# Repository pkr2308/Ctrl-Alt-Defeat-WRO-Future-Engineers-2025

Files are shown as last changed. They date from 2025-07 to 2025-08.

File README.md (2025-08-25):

# This repository has been moved to [CmdOptDefeat/fe25](https://github.com/CmdOptDefeat/fe25)

<picture>
  <source media="(prefers-color-scheme: dark)" srcset="https://github.com/pkr2308/Ctrl-Alt-Defeat-WRO-Future-Engineers-2025/blob/main/repo-assets/logo/ctrlaltdefeat-no-glow-no-bg-4096.png">
  <source media="(prefers-color-scheme: light)" srcset="https://github.com/pkr2308/Ctrl-Alt-Defeat-WRO-Future-Engineers-2025/blob/main/repo-assets/logo/ctrlaltdefeat-no-glow-no-bg-dark-4096.png">
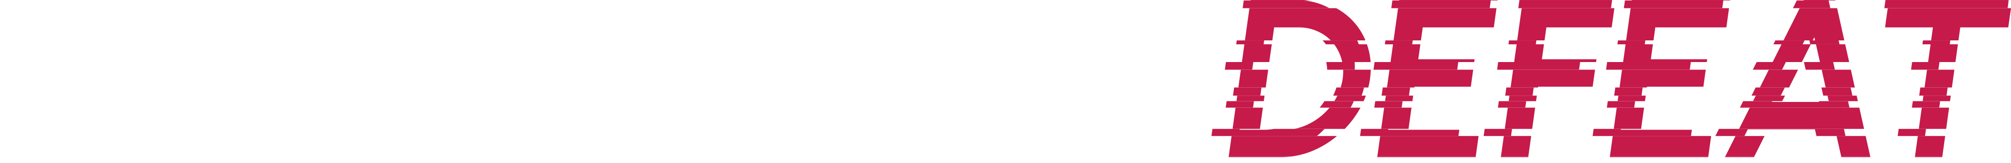
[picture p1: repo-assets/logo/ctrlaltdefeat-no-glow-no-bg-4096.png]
CTRL+ALT+DEFEAT Logo (updates based on your theme!)
  
</picture>

<br><br>Welcome to the repository for our entry in the WRO Future Engineers 2025 competition!
We are a team of 2 aspiring engineers building an autonomous robotic car using Raspberry Pi 5 & RP2040, equipped with various sensors and custom designs.

# About the Team
Adbhut Patil: TODO: expand 10th standard, interested in electronics, programming, aviation

Pranav Kiran Rajarathna: Pranav is currently sudying in the 11th grade(PCMC combination) and has been interested in Robotics for several years . He has participated in WRO in other categories in the past years. He was also part of Coding club in his school and built a few robotics projects for school events. His other interests include maths, physics, numismatics and history.

| __Team Photo__ |
|:-----------:|
|Team Photo|
| __Picture: Pranav (Left) and Adbhut (Right)__ |

# Project Overview
This project is our official entry for the Future Engineers category at the World Robot Olympiad 2025. Our goal is to construct a self-driving vehicle capable of navigating the track in both the Open and Obstacle Rounds. The programs are written in C++ and Python in the VSCode IDE, with the PlatformIO extension. OpenCV is used with the Raspberry Pi for object detection and navigation. This repository contains the programs, hardware description, schematics and design files of our solution.

# Hardware Components
- __Compute:__ Raspberry Pi 5 (main computer), Raspberry Pi 2040 (Waveshare RP2040-Zero, real-time control)
- __Sensors:__ 1D and 2D LiDAR, IMU, rotary encoders, Picamera
- __Actuators:__ N20 geared DC motor with encoder, MG996R 180° servo
- __Chassis:__ Commercially available base with 3D-printable additions (3D-design files included)
- __Electronics:__ Custom peripherals interface PCB for reliable connections to sensors

Note: The whole readme file is massive.
See [this section](https://github.com/pkr2308/Ctrl-Alt-Defeat-WRO-Future-Engineers-2025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) for more details about sensors on the peripherals interface board, and <link> for details about the RPi 5 and its sensors.

# Repository Structure
- [design-files](https://github.com/pkr2308/Ctrl-Alt-Defeat-WRO-Future-Engineers-2025/tree/main/design-files) : Contains the Bill of Materials, 3D-printable design files and hardware. Pictures and description of the robot and components are included.
- [initial-tests](https://github.com/pkr2308/Ctrl-Alt-Defeat-WRO-Future-Engineers-2025/tree/main/initial-tests) : Intial tests on various sensors to ensure accurate data collection and basic object detection algorithm.
- [hw](https://github.com/pkr2308/Ctrl-Alt-Defeat-WRO-Future-Engineers-2025/tree/main/hw) : Contains schematic and PCB files for the peripherals interface board.
- [sw](https://github.com/pkr2308/Ctrl-Alt-Defeat-WRO-Future-Engineers-2025/tree/main/sw) : Contains PlatformIO project for the peripherals interface board.
- [open-round](https://github.com/pkr2308/Ctrl-Alt-Defeat-WRO-Future-Engineers-2025/tree/main/open-round) : It contains the program files for the open round over various iterations and hardware setups. The final open round program is found in `sw/peripherals-board/src/divers`
- [repo-assets]() :
- [obstacle-round](https://github.com/pkr2308/Ctrl-Alt-Defeat-WRO-Future-Engineers-2025/tree/main/obstacle-round) : 
- [test-data-recordings/open-round](https://github.com/pkr2308/Ctrl-Alt-Defeat-WRO-Future-Engineers-2025/tree/main/test-data-recordings/open-round) : It contains data logs from various open round tests

> [!NOTE]
> Random files called `.lgd-nfy0` may be seen sometimes in varioues places. These were probably created by a typo a long time ago, and despite repeated deletion, they keep spawning everywhere in the Pi's cone of the repo! Just ignore them, if they occur. 

# System Architecture 

-	Raspberry Pi 5: It uses ROS2 and handles more complex tasks like object and colour detection, route planning, and the 2D LiDAR
-	RP2040 (Pi Pico): Handles real-time tasks (motor PID, encoder feedback, servo control, IMU, 1D LiDAR)
-	LiDARs: Used for detecting turn direction, obstacles and in parking
-	IMU: Gives yaw (and other orientations) of the robot in [0,360)
-	Motor/Servos: PWM and PI controls respectively for movement using sensor data, coordinated by the RP2040

## Mobility

- A commercially available metal [chassis base](https://www.elecrow.com/4wd-smart-car-robot-chassis-for-arduino-servo-steering.html) has been used with custom designed and printed parts. This chassis was selected mainly for its good steering system, mobility and customisabilty (there are lots of through holes through the base-frame). While the steering was retained, the remaining parts were custom designed.
- A link based steering system is used in the robot with a link-rod between the front wheel joints and another between a wheel joint and the servo. This steering system has been taken from the chassis without much modification due to its precision. A MG996R 180° servo has been used for the steering due to its high torque and accuracy, which improve mobility. 
- A single axle rear drive train is used for driving is used. A 200RPM N20 motor is used due to its speed and decent torque. A 1:1 gear ratio is used with a pair of brass gears. Bearings are used on the rear axle for smooth movement. A custom [rear drive holder](https://github.com/pkr2308/Ctrl-Alt-Defeat-WRO-Future-Engineers-2025/blob/main/design-files/N20%20Motor%20Holder.stl) is used to house all these parts.
- Both the servo and N20 motors are connected to the peripherals board. The servo is controlled using the standard library, while PWM is used for speed control of the motor.
- Turning Radius: Optimized for narrow WRO track corners, and is 32-33 cm.
- Build Choice Reasoning: Offers realistic car-like dynamics, ideal for FE challenge simulation.
[Design files](https://github.com/pkr2308/Ctrl-Alt-Defeat-WRO-Future-Engineers-2025/tree/main/design-files) contains all the other custom 3D-Design files (created on [TinkerCAD](https://www.tinkercad.com)) for mounting various compnents and systems onto the base chassis and one another.
[Robot assembly](https://github.com/pkr2308/Ctrl-Alt-Defeat-WRO-Future-Engineers-2025?tab=readme-ov-file#robot-assembly) instructions are below.
- Improvements: 
1. A uniform steering system. In the current model, the servo has to turn a greater angle left than right for the same angles of the wheels in each direction. This complicates driving algorithms to some extent. A better, but equally smooth steering system, maybe a rack-and-pinion, will solve these issues.
2. Better gear train. The current gears, though made of brass wear down quite easily for some unidentified reason. This causes slipping if there is more wear.
3. Reducing the turning radius. The current bot, while quite manoeuvrable has a large turn radius (almost 33-34cm). Reducing this would make taking tighter turns possible, improving error margins in the obstacle round. This can be done by bringing the drive train forward.

## Power

- A [Waveshare UPS Hat E](https://www.waveshare.com/wiki/UPS_HAT_(E)) is used for powering the robot. It uses 4 4000mAH 3.6V 21700 Li-ion batteries. (Different battery capacities may be used). All outputs are at 5V.
- The Pi is powered at a stable 5V via the POGO pins on the UPS Hat. The PiCamera and RPLidar are power from the Pi.
- The RP2040 and all connected sensors are powered through a USB A-C cable from the Pi to it.
- The total current draw for the obstacle round is around 600-630mA, and around 250-300mA for idle with the Pi.
- The peripherals board gets power directly from the UPS Hat through a USB-A cable that has been cut to get the power wires. This powers only the rear motor and steering servo.
- Improvements:
1. The UPS Hat that we are using has a weird anomaly. Although the batteries will have good voltage output and detected capacity, it will show the net remaining capacity to be very low. We have edited the code of the UPS library to not allow it run `sudo poweroff` when it misdetects such a situation.
2. Maybe not have the small switch on the board; closing it will cause these 2 systems to be connected, which could lead to some bad outcomes!

## Sensors

- __TFLuna LiDAR:__ These are 1D-LiDARs that are used to measure distances to the front, left, right (for driving) and back(parking) of the robot. They are connected to the RP2040. A separate section has been designed at the front of the robot to house all four LiDARs. Each LiDAR has 5 wires, grouped into 4+1 (I2C + GND) going into the peripherals board. These LiDARs were selected for their accuracy, small size and ease of use.
- __BNO055:__ This is the IMU we are using for orientation due to its reliability, accuracy and simplicity of use. It is connected to the RP2040, and is directly slotted into the peripherals board.
- __nRF24L01:__ This is the wireless module used for wireless communication during testing and debugging with the RP2040. Another custom module (telemetry board) is made for receiving the data. (Note : This is not plugged in for actual rounds). It is directly slotted into the peripherals board.
- __Motor encoders:__ The encoders give ticks each time they are trigerred by rotation of the motor shaft. Data from it is used for distance calculations. In our case, about 43 ticks corresponds to 1cm. The 4 encoder wires are grouped together and connected to the peripherals board.
- __Raspberry Pi Camera Module 3 Wide:__ It is used with the Pi for detecting the an obstacles. The camera is secured at four points for greater stability. With only two connection points, the camera could be easily turned due to the material properties of the Camera to Pi 5 connection wire. The higher mounting location allows it to detect obstacles from a large distance (almost 2m!) and plan accordingly. The Wide lens allows for a greater field of view. The NoIR version used to give odd red patches due to the lack of the IR filter in some test cases.
- __RPLidar A1:__ It is a 2D-LiDAR. It was supposed to be connected to the Pi and give distance all around the robot. However, we could not get it work Raspbian or any other OS. (It worked well with ROS though!) So, it is basically dead weight!
- Improvements: 
1. The RPLidar doesn't work well with the standard Raspbian OS on the Pi or with a computer, with values for many angles returned zero or being frozen. It seems to work fine on ROS though. Not sure what the issue is, but resoving this can improve ease of programming.
2. The 1D LiDARs are quite expensive. Ultrasonic sensors would have done for the sides.
3. The BNO055 does clock stretching, which causes issues on the I2C buses of most microcontrollers (thankfully not the RP2040). It also has a slight drifting tendency of a few degrees after a round. A IMU that does not have these issues and is easy to use will be more accurate and more flexible in use.

The [Bill of Materials](https://github.com/pkr2308/Ctrl-Alt-Defeat-WRO-Future-Engineers-2025/blob/main/design-files/Bill%20of%20Materials.md) contains all necessary parts/components and their sources.

## Obstacle Management

- This is done mainly using the camera feed from the PiCamera 3 Wide. The NoIR version tends to give red spot in places with lots of light due to lack of IR filter, which made it incompatible for this case.
- The OpenCV library (in Python3) is used for all the image manipulation and data extrapolation. HSV mode has been used for all the detecting, while images arer displayed in RGB. Sometimes, red may appear as blue due to use of BGR format used by camera to rercord. This is of no consequence, since it does not affect detection itself.
- Initially, the colour ranges for the obstacles, parking walls and side walls are identified. Interestingly, in our case, the 'magenta' parking walls show up as pure red.
- First, the region of interest (ROI) is taken as the bottom half of the feed (this is for our camera placement. May vary for other setups).
- Then, coloured masks (one each for red and green) are applied, followed by OpenCV's controur detection to detect surfaces. Data like position, height and width of the contours may be obtained from the other OpenCV methods.
- If the contours detected meet the required criteria (like size, height-width ratio), they are classified as obstacles. For our benefit, rectangles are drawn around the obstacles.
- Using the data available, including obstacle position, yaw and distance travelled, the required steering is calculated to pass the obstacle on the correct side, when not at a turn (Red - right, green - left)
- When the side chosen is preceded by a turn, the turn is initiated at a predefined distance from the wall ahead. (Ex: Clockwise round, green -> turn early)

Improvements:
1. The RPLidar might have been used effectively with better drivers with the standard Raspbian OS.
2. A more accurate formula to convert y-coordinate of obstacle obtained by the camera into actual distance

# Robot Assembly

It will be helpful to refer to the pictures of the completed model for the following steps. Most screws used are of 3M type (3mm dia.). At some places in our robot, internal hex screws are used in places where plus(+) screws of the right length were not available.
1. Add the front wheels and steering link to the robot
2. Attach the servo motor and connect it to the steering link
3. Print all design files
4. Attach the N20 motor onto the rear drive with brackets. Fit a gear onto the motor.
5. Cut the rear axle to the appropriate length (around 96mm) and attach the rear axle with wheels and gear onto the rear drive.
6. Mount the rear drive onto the chassis.
7. Attach 6 pillar screws of length 26mm in the back and 2 of length 22mm in the front (adjacent to the servo)
8. Attach the middle plate at the 6 rear points, but not at the front. The peripherals board may be screwed on using 4 pillar screws.
9. Attach the TFLuna LiDARs to the front LiDAR holder section, followed by the RPLiDAR (remember to connect the USB adapter) with 22/24 mm screw pillars. Screw in the front points.
10. Attach the LiDAR holder section to the front of the chassis.
11. Attach the additional support section for the LiDAR holder to the 2 front middle plate points and 2 rear RPLidar points.
12. Screw in the RPLidar's extra micro-USB pin extender to the support section
13. Attach the two PiCamera holder parts to the rear of the Lidar support section, and screw in the camera (2M screws and nuts are needed)
12. Attach the top-most Raspberry Pi and UPS platform to the rear with screw pillars.
13. Attach the rear lidar holder with the rear lidar attached to it
14. Attach the Raspberry Pi with the UPS Hat to the top.
15. Make all wired connections by referring to schematic files.

# Peripherals Interface Board
Peripherals Interface Board - Top

The peripherals interface board goes between the Raspberry Pi and vehicle hardware. The board talks to three 1d TFLuna LiDARs, a 9-axis BNO055 IMU, the motor encoder, the drive motor, and the steering servo. It talks to the Pi over USB.

## Hardware
The board is a two-layer, 1.6 mm thick PCB designed in [KiCad](https://kicad.org) and manufactured by [Robu](https://robu.in).
TODO: Expand

## Software
The interface board was programmed in C++, with the C++ SDK from Raspberry Pi for the RP2040 chip. Code was flashed using the PlatformIO extension for the VSCode editor.

The codebase is designed to be modular, with easily swappable drivers for hardware abstraction. Algorithms do not need to know about specific hardware protocols or constraints

`main.cpp` loads in drivers, which implement virtual interface classes. `main.cpp` then initialises everything, and in a loop, gets data from the `SensoorManager`, passes that data to our drive algorithm, and outputs it to the `TargetController`, which commands the motor and steering servo.
Drivers are in `/src/drivers`, Interfaces are in `/src/interfaces/`, and utilities are in `/src/utils/`.

### Code Development Standards
To ensure easily testable, upgradeable, and clean code, a few standards were adhered to when writing code for the interface board.

- `main.cpp` must be as clean as possible.
  - Logic and code flow must be easy to understand.
- All hardware-specific things should be done inside a driver.
- Drivers must take in a standard unit as their input.
  - Drivers must not take in [magic numbers](https://en.wikipedia.org/wiki/Magic_number_(programming)).

TODO: Finish writing this

### Drivers
> [!NOTE]
> Hardware revision 1 drivers are incomplete, as the peripherals baord codebase was partly written when the switch from the prototype interface and the PCB occured, and drivers from that point on were only for the PCB (hardware revision 2).
A list of implemented drivers:
- `hwrev2_imu` : Implements `ISensor`. Driver for the BNO055. Gets orientation data processed by the BNO055's internal microcontroller.
- `hwrev2_lidar` : Implements `ISensor`. Driver for the TFLuna LiDARs. Returns a [0, 259] of distance data. The three LiDARs are mapped to `0`, `90`, and `270`. (This is a remnant of the original plan of connecting the RPLidar to the peripherals board, instead of to the Pi.)
- `hwrev2_motor_driver` : Implements `IMotorDriver`. Driver for the TB6612FNG dual-channel H-bridge motor driver. The driver only supports driving a single channel on the T66612FNG.
- `hwrev2_rf24_communication` :  Implements `ICommunication`. Driver for the nRF24L01+ radio used during development. Transmits vehicle data and gets commands from another nRF24L01+, connected to a computer.
- `hwrev2_single_lidar_open_round` : Implements `IDriveAlgorithm`. A port of our open round test algorithm. The name is misleading, the algorithm uses all three TFLunas.
- `hwrev2_steering_driver` : Implements `ISteeringDriver`. Driver for the MG996 steering servo. Takes in a degree input and coverts it to a 0-180 command with a conversion constant.
- `hwrev2_target_control` : Implements `ITargetControl`. Takes in a `VehicleCommand`, and either passes it directly through to the `ISteeringDriver` and `IMotorDriver`, or passes the command through a PID controller first.
- `hwrev2_uart_logger` :  Implements `ILogger`, Takes in a sender, message type, and a message string
- `hwrev2_vehicle_speed` : Implements `ISensor`. Gets vehicle distance from the motor encoder. Calculates speed using time between pulses.

### Interfaces

Interfaces are virtual classes which define certain functions. Drivers implement these classes. Code calls functions defined in the interface virtual class.

- `IDriveAlgorithm` : Takes in a `VehicleData` object, and returns a `VehicleCommand` object.
- `ILogger` : Constructs a message and prints it out on a UART bus. Takes in a sender string, a log type (information, warning, error) and the message.
- `IMotorDriver` : Takes in a speed value and outputs to a motor driver.
- `ISensor` :  A generic sensor object. Returns a vector of `SensorData` objects.
- `ISteeringDriver` :  Takes in a wheel steering angle, outputs to a steering mechanism.
- `ITargetControl`: Takes in a `VehicleCommand`, outputs to a motor and steering driver.

### Managers

Managers are classes that handle certain aspects of the vehicle. Certain structs have their header files in the `/src/managers` folder, even though they are not classes.

- `VehicleConfig` :  A struct containing information about the vehicle. A `VehicleConfig` struct is passed to all drivers asnd managers.
- `SensorData` :  A struct containing fields for all data that can be collected by the vehicle, and an enum which tells the caller what fields are being used.
- `SensorManager` :  A class which takes in an arbitrary number of sensors, collects data from them, and processes them into a `VehicleData` struct.
- `SensorStatus` :  A (currently unused) enumeration which defines keys for states a sensor can be in. 
- `Vec3f` :  A struct of three double-precisionn floating point numbers, used to represent three-axis values.
- `VehicleCommand` :  A struct defining a target speed and yaw value for the vehicle. Returned by a drive algorithm, passed to a `ITargetController`.
- `VehicleData` :  A struct containing processed vehicle data. Returned by a `SensorManager`.

## Utilities

- `SchedulerTask` : A class which calls a function periodically.
- `Schedular` : A class which takes in an arbitrary number of `SchedulerTask`s, and updates them.

# Raspberry Pi System

The Raspberry Pi system handles most tasks for the obstacle round, including unparking, obstacle detection and navigation.

## Raspbian Setup

We are using Raspbian Bookworm.
Run the following commands in the terminal
- $`sudo chmod 0700 /run/user/1000`
- $`sudo apt install software-properties-common`
- $`sudo apt install python3-launchpadlib`
- $`sudo apt install code`
- $`sudo apt upgrade code`
- $`sudo apt install idle3`
- $`sudo apt install python3-opencv`
- $`sudo apt install -y python3-libcamera python3-pyqt5 python3-picamera2`
- Refer [here](https://www.waveshare.com/wiki/UPS_HAT_(E)) to install UPS library to show details about the batteries.
- If the Pi is accidentally shut down, and git is not working, run the following: 
1. $`find .git/objects/ -type f -empty | xargs rm` - Cleaning
2. $`git fetch -p` - Restore missing objects
3. $`git fsck --full` - Verify
- It is advised to have RPiConnect for easy connection to the Pi.
- This reposittory is cloned on the Pi and the obstacle round program is added to the startup sequence.

## Adding Programs to Startup

The method used here involves running executables on startup. Refer [`initial-tests/startup-test/`](https://github.com/pkr2308/Ctrl-Alt-Defeat-WRO-Future-Engineers-2025/tree/main/initial-tests/startup-test) for the code.
1. Create the python file
2. Create a launcher script, like the one in the initial test file, that ends in `.sh`. Ensure the launcher is working with `./(launcher-name).sh` in its directory.
3. In the launcher script, navigate to the directory of the python file and run it with `sudo python3 (file-name).py`. Then return to user directory
4. In the directory with launcher script, make it executable by running `sudo chmod 755 (launcher-name).sh`
5. Run `sudo crontab -e` (you can use nano to edit it), and add `@reboot sh /home/(user)/(path to launcher)/(launcher-name).sh` at the end.
6. Restart the Pi (`sudo reboot`) to check if it works.

## PiCamera 3

The Raspberry Pi Camera Module 3 Wide is used for obstacle detection. It is placed high up to have a good view. (We actually only use the bottom half of the frame!)

## Serial Communication

The Pi communicates with the RP2040 over the serial. When the Pi sends a command (speed and steering), the RP2040 sends back data (like yaw, lidar distance, turn direction etc.)

# Open Round

Refer to `sw/peripherals-board/src/drivers/hwrev2/hwrev2_single_lidar_open_round.cpp and .hpp` files for program.

## Header File

Public includes the logger (for debugging), vehicle command (for driving) and sets direct control of servo (A target yaw value is generally given). Private includes setup of variables for driving, turning, servo, IMU, 1D LiDARs and IMU-based straight follower. 

## Implementation File

### Initialisation
- Sets up logging
- Sets initial speed and steering

### Turn Detection & Execution:
- Uses front LiDAR to detect when to start a turn (if obstacle is close).
- Decides turn direction (left/right) based on side LiDARs (First turn only)
- Turns are started considering factors of distance available, yaw, current section and distance travelled. 
- Adjusts steering (servo position) during turn based on yaw and for greater smoothness.
- After each turn, resets variables and prepares for the next segment. Target yaw and threshold distance may be altered for better accuracy and counter drifting.
- The idea to stick to the outer wall, so even with randomisation, the extended inner wall is not hit

### Straight Movement:
- When not turning, uses gyro (yaw) to follow a straight path.
- Applies proportional-integral correction to steering for accurate straight-line travel.

### Turn Direction Logic:
- Chooses clockwise or anticlockwise based on which side has more open space (LiDAR difference).
- Sets different thresholds for smoother turns depending on direction.

### Stopping 
- Counts turns; after 12 turns (3 rounds), slows down and stops at the start section.

## Flow
1. Start moving straight.
2. Decide turn direction using side LiDARs. (For first turn only)
3. Detect distance to wall ahead with front LiDAR.
4. Execute turn when condition are met, adjust steering and target yaw.
5. After turn, resume straight movement with PI control.
6. Repeat for 3 rounds (12 turns).
7. After final round, slow down and stop in the start section.

# Acknowledgements

We would like to thank
- YoLabs Team:
- Raspberry Pi Foundation:
- OpenCV :

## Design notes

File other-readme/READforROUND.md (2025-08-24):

__Remember to read this document before the round__
Checklist of things to do:
- Check battery level. Atleast 150-200 min remaining
- RP2040 is correctly inserted. Loose connections may be there
- Check if any errors are logged over debug port
- check if warning light indicates failure
- Connect the RP2040 to Pi's USB2 (black) ports
- Check if light on encoders turns on - loose connection may be there
- Check if wheels are able to turn freely without touching anything else
- Ensure back lidar is in proper place, and not at an angle
- Ensure OpenCV windows are not created for the obstacle round (even for practices); merely record the videos!

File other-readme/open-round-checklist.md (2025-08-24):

# Open Round Checklist
## Things to do right before / as vehicle is powered up for the open round

### Before round starts
| Item | Action |
| ---- | --- |
| RPi UPS Module batteries | Fully insert |
| RPi UPS Module power switch | Off |
| Peripherals Interface power switch | On |

### Powering vehicle on
| Item | Action |
| ---- | --- |
| RPi UPS Module power switch | On |
| Peripherals Interface start button | Press |

### Peripherals Interface LED Colors
| Color | State | Indication |
| ----- | ----- | --- |
| Blue | Steady | Sensors are being calibrated
| Green | Steady | Sensors are calibrated, Peripherals Interface has control |
| Green | Blinking | RPi 5 has control |
| Amber | Blinking | Sensors failed to calibrate/are not detected

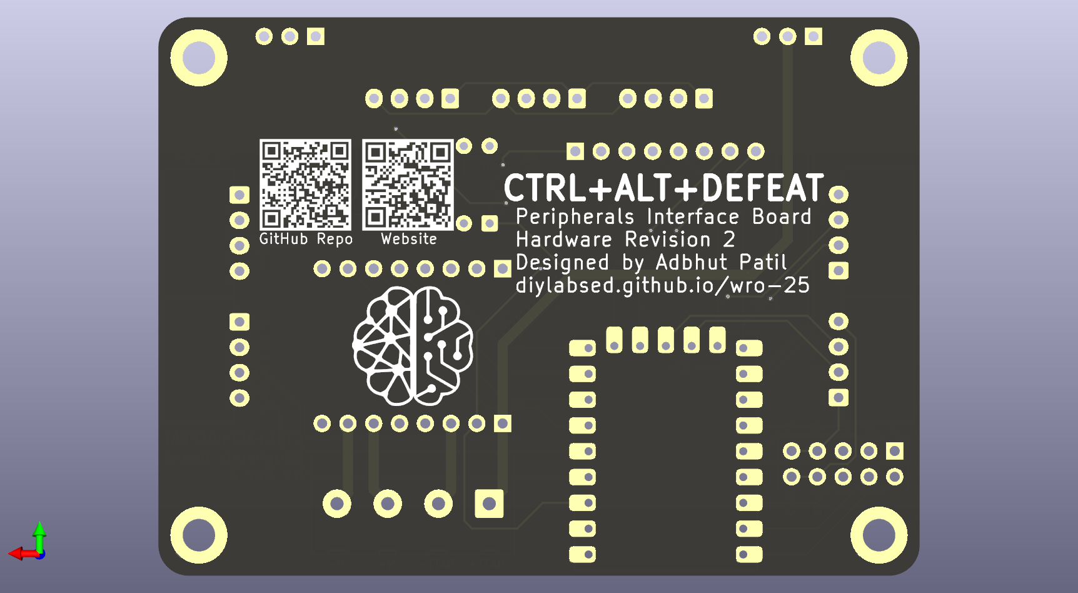
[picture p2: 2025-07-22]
hw/peripherals-board-v2/renders/batch2/back-orthographic-non-raytraced.png

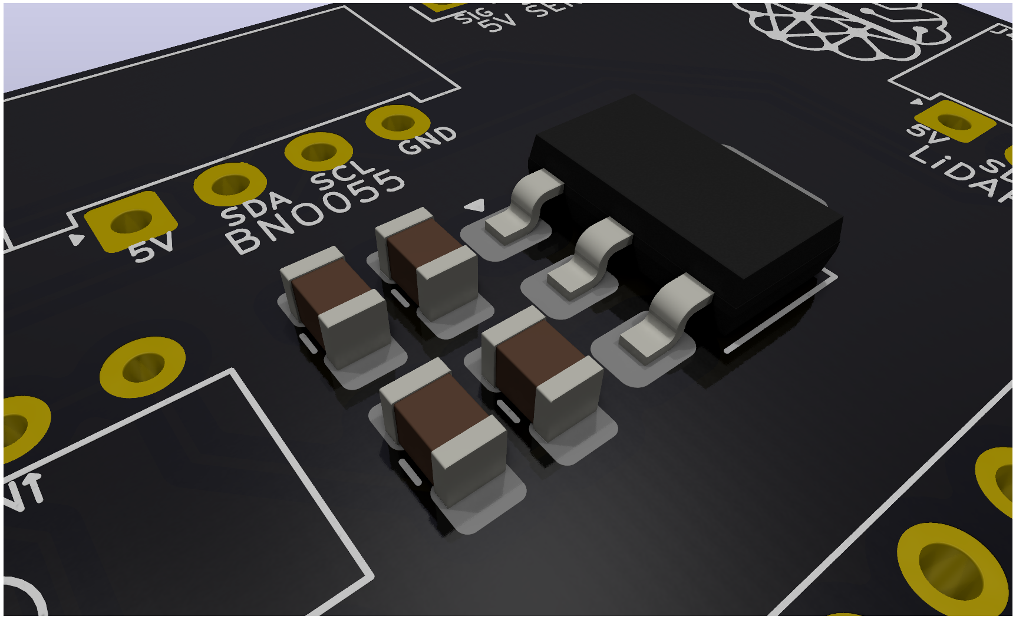
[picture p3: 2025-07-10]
hw/peripherals-board-v2/renders/batch1/front-voltage-regulator-floor.png

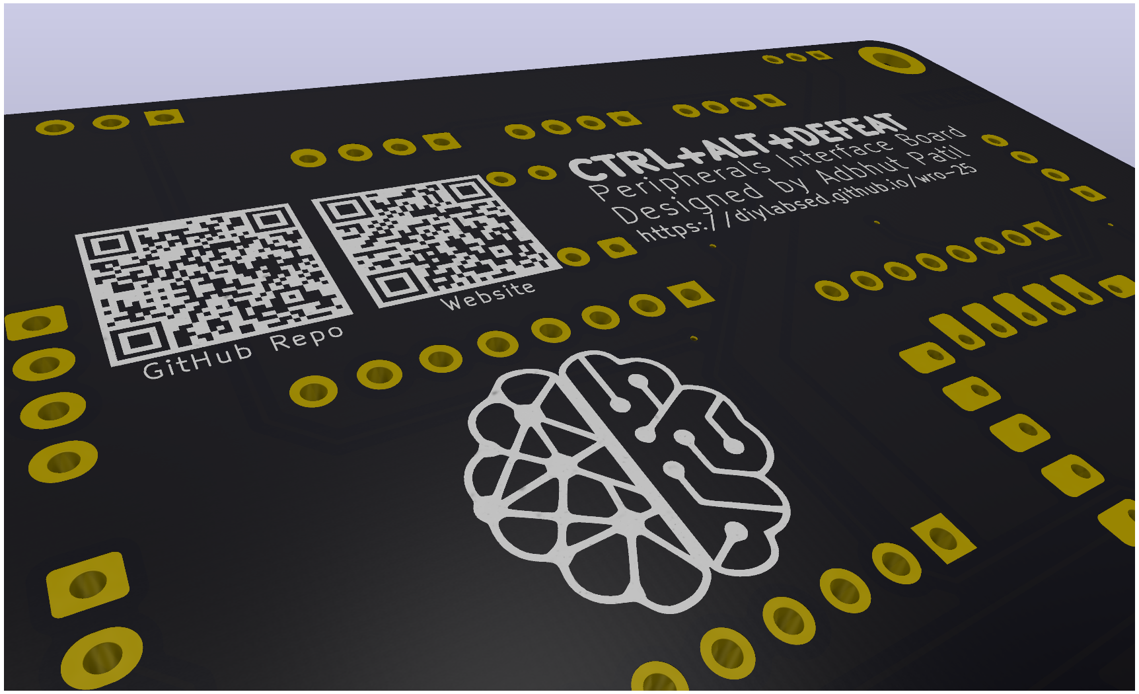
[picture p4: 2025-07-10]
hw/peripherals-board-v2/renders/batch1/back-angled-floor.png

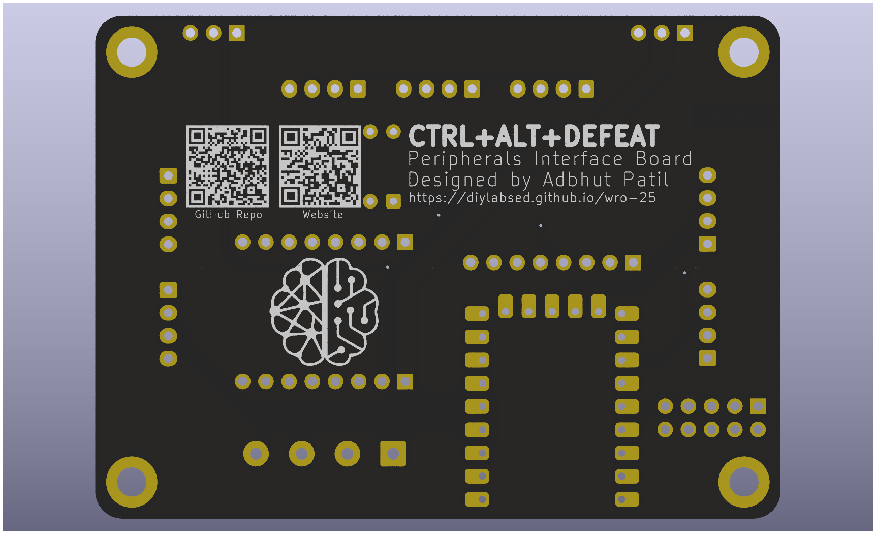
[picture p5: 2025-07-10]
hw/peripherals-board-v2/renders/batch1/back-orthographic.png

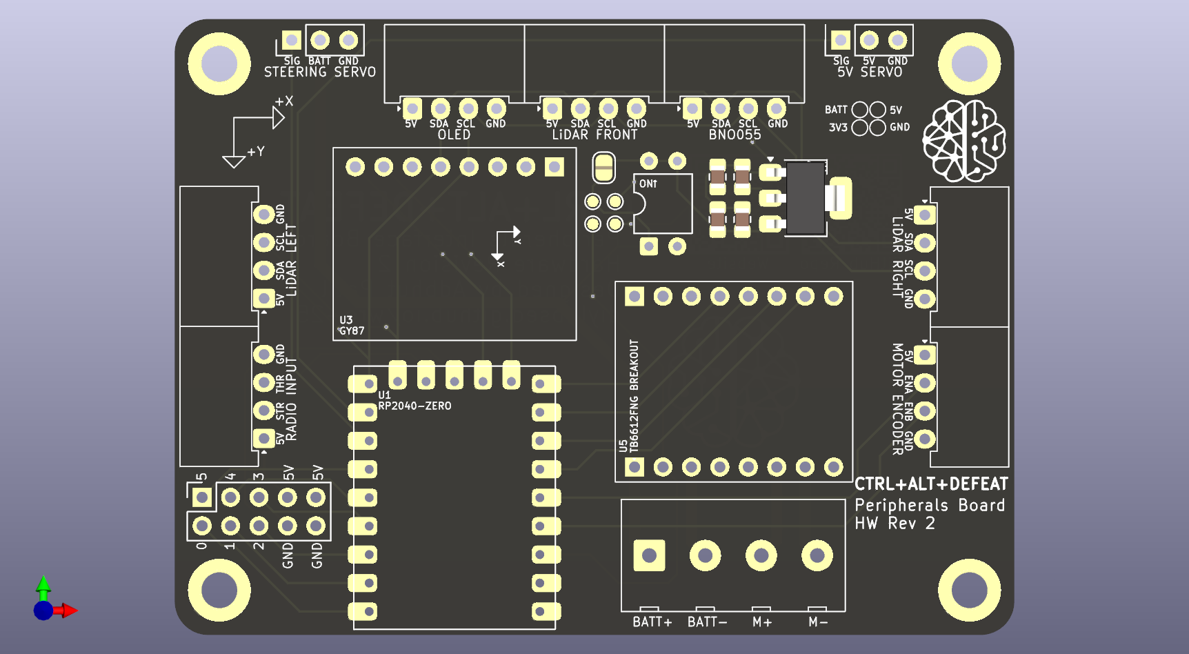
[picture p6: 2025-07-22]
hw/peripherals-board-v2/renders/batch2/front-orthographic-non-raytraced.png

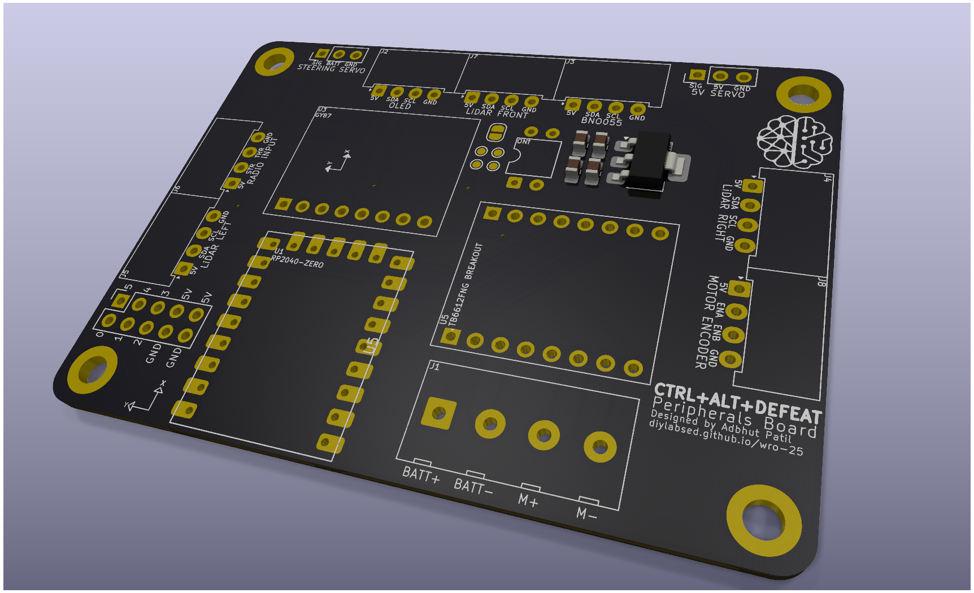
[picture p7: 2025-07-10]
hw/peripherals-board-v2/renders/batch1/front-angled-floor.png

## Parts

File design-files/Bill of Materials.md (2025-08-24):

# Bill of Materials

## Chassis
| Item | Part No. | Quantity | Notes/Description | Link | 
|:---:|:---:|:---:| :---:| :---:|
| N20 Motor Mounting Bracket | - | 1 | Hold N20 motor in place in the rear drive section | [Product Link](https://robu.in/product/mounting-bracket-n20-micro-gear-motors) |
| Gears | Metal 24 tooth spur gear, 3mm | 2 | Used in the rear drive | [Product Link](https://robu.in/product/metal-48p-spur-gear-24t/) |
| Rear Drive Section | Custom design | 1 | Holds rear axle and N20 motor and connection through gear | [Link to Design](https://github.com/pkr2308/Ctrl-Alt-Defeat-WRO-Future-Engineers-2025/blob/main/Design%20Files/N20%20Motor%20Holder.stl) |
| Shaft | 3mm | 1 | Used as rear drive shaft |
| Chassis | RBP68138C | 1 | Front steering and single axle rear drive | [Product Link](https://www.elecrow.com/4wd-smart-car-robot-chassis-for-arduino-servo-steering.html) |
| 18650 Batteries | 3.7 V Different mAH options availaible | 2 | Provide power | [Product Link](https://robu.in/product/dmegc-inr18650-26e-3-7v-2600mah-li-ion-battery) |
| 21700 Batteries | 3.6 V Used with UPS Hat to power the Pi | 4 | Provide power | [Product Link](https://robu.in/product/bak-nmc-n21700cgp-3-6v-4000mah-10c-li-ion-battery) |
| Battery Holder | - | 1 | Hold the 18650 batteries, and has an on/off switch | [Product Link](https://robu.in/product/18650-x-2-battery-holder-with-cover-and-on-off-switch) |
| Custom Designed Parts | - | 1 each | Used for attaching various components to the robot |[Design files](https://github.com/pkr2308/Ctrl-Alt-Defeat-WRO-Future-Engineers-2025/tree/main/Design%20Files) |
| Miscellaneous | - | - | Wires, Screws, Pillar Screws etc. | [Pillar Screws](https://robu.in/product/pro-range-120pcs-m3-hexagon-copper-pillar-screw-kit/) |

## RP2040 System
| Item | Part No. | Quantity | Notes/Description | Link | 
|:---:|:---:|:---:| :---:| :---:|
| RP2040 | Waveshare RP2040-Zero | 1 | Real time control of motors, sensors | [Product Link](https://robu.in/product/waveshare-rp2040-zero-without-header/) |
| Peripherals Board | Custom design | 1 | Various compnents may be easily connected to RP2040 | [Link to Design](https://github.com/pkr2308/Ctrl-Alt-Defeat-WRO-Future-Engineers-2025/tree/main/hw/peripherals-board-v2) |
| 1D LiDAR | Benewake TF-LUNA Micro | 4 | Finding distances to front, sides and back of robot | [Product Link](https://robu.in/product/benewake-tf-luna-lidar-distance-sensor/) |
| 1D LiDAR Connectors | 28AWG 1.25mm 6 Pin Female Connector | 4 | Connect LiDAR to peripherals board | [Product Link](https://robu.in/product/a1251-06y-1-25mm-6-pin-female-housing-connector-with-300mm-wire30-awg/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) |
| IMU | BNO055 | 1 | Obtaining yaw readings | [Product Link](https://thinkrobotics.com/products/9-dof-absolute-orientation-bno055-sensor) |
| Wireless Radio Transciever (Optional) | NRF24L01 Wireless Transceiver | 1 | Wireless communication during testing and debugging | [Product Link](https://robu.in/product/m177-nrf24l01-2-4ghz-antenna-wireless-transceiver-module)
| Motor Driver Board | TB6612FNG | 1 | Control N20 Motor | [Product Link](https://robu.in/product/motor-driver-tb6612fng-module-performance-ultra-small-volume-3-pi-matching-performance-ultra-l298n/) |
| Motor with Encoder | N20 6V 200RPM Micro Metal Gear Motor With Encoder | 1 | Rear driving motor | [Product Link](https://robu.in/product/n20-6v-200rpm-micro-metal-gear-motor-with-encoder/) |
| Servo Motor | MG996R 180° | 1 | For steering | [Product Link](https://robocraze.com/products/mg996r-servo-motor?variant=40192896368793) |
| Wire Management | 3, 4 Pin JST-XH 2.5mm wafers and housing; DuPont 2.54mm female headers | 1, 6, 34 | Connect various components easily onto peripherals board | - |
| Screw Terminals | 2 Pin Screw Terminals | 2 | Connecting power and motor pins to peripherals board | [Product Link](https://robu.in/product/xy128vc-5-0-xinya-2-pin-screw-terminal-blockgreen) |

## Raspberry Pi 5 System
| Item | Part No. | Quantity | Notes/Description | Link | 
|:---:|:---:|:---:| :---:| :---:|
| Raspberry Pi 5 | Raspberry Pi 5 Model 8GB | 1 | Object and lane detection and route planning | [Product Link](https://robu.in/product/raspberry-pi-5-model-8gb/) |
| Cooler for Pi | Raspberry Pi 5 Active Cooler | 1 | Cool the Pi when running | [Product Link](https://robu.in/product/official-raspberry-pi-5-active-cooler) |
| Picamera | Pi Camera Module 3 - Wide | 1 | Object, colour detection | [Product Link](https://robu.in/product/raspberry-pi-camera-module-3-wide) |
| Picamera Wire | Raspberry Pi 5 Camera FPC Cable 300mm | 1 | Connects PiCamera to RPi 5 | [Product Link](https://robu.in/product/official-raspberry-pi-5-camera-fpc-cable-300mm/) |
| 2D LiDAR | SLAMTEC RPLiDAR A1 360° | 1 | Object detection | [Product Link](https://robu.in/product/rp-lidar-a1m8-360-degrees-laser-range-finder/) |
| USB A - USB C Cable | - | 1 | Connect the Pi to the RP2040 | - |
| USB A - MicroUSB Cable | - | 1 | Connect the RPLidar to the Pi | - |
| UPS Hat | WaveShare UPS Hat E | 1 | Used power constant 5V supply to RPi | [Product Link](https://robu.in/product/ups-hat-e-for-raspberry-pi/) |

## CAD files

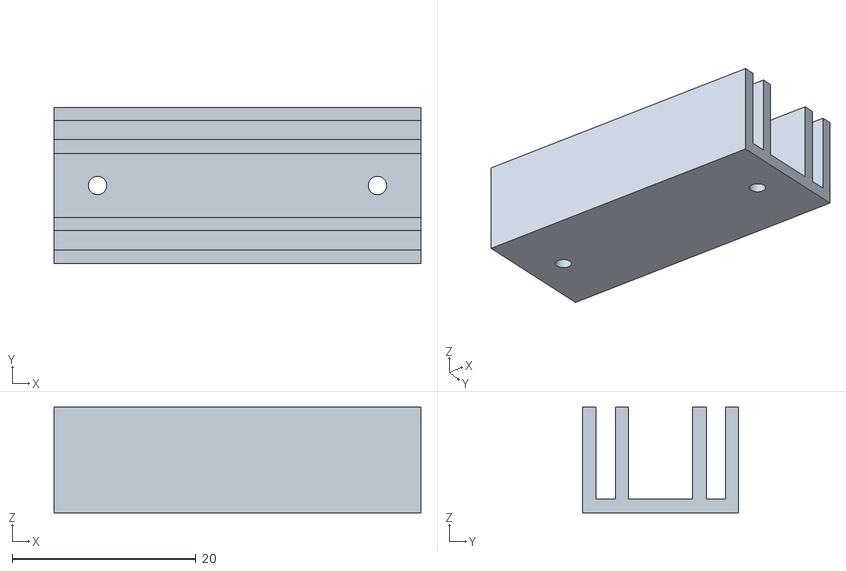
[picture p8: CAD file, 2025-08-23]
design-files/Rear Lidar Mount.stl
40.0 x 17.0 x 11.5

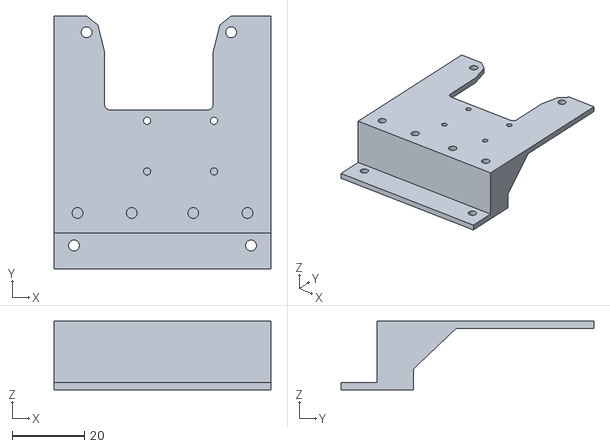
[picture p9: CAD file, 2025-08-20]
design-files/RPLidar Support.stl
60.0 x 70.0 x 19.0

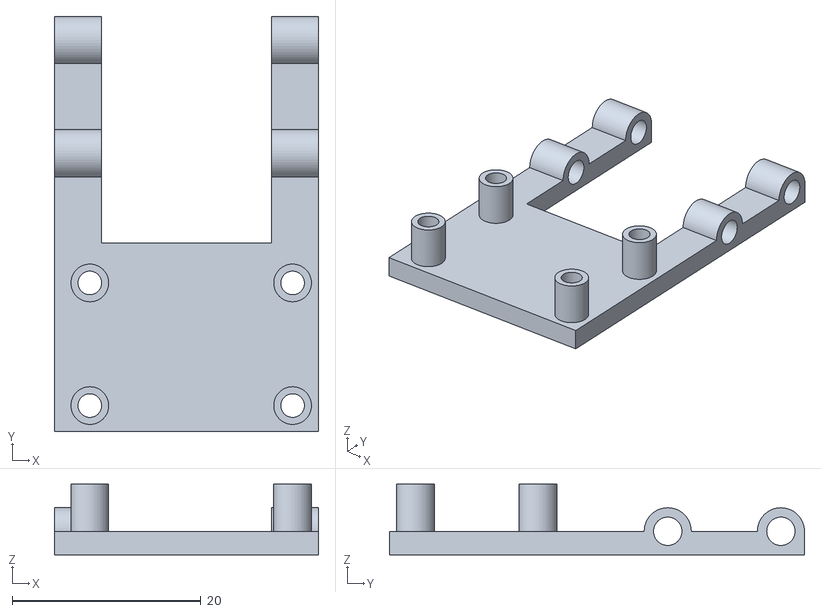
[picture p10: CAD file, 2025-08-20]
design-files/PiCam3 Holder.stl
28.0 x 44.0 x 7.50

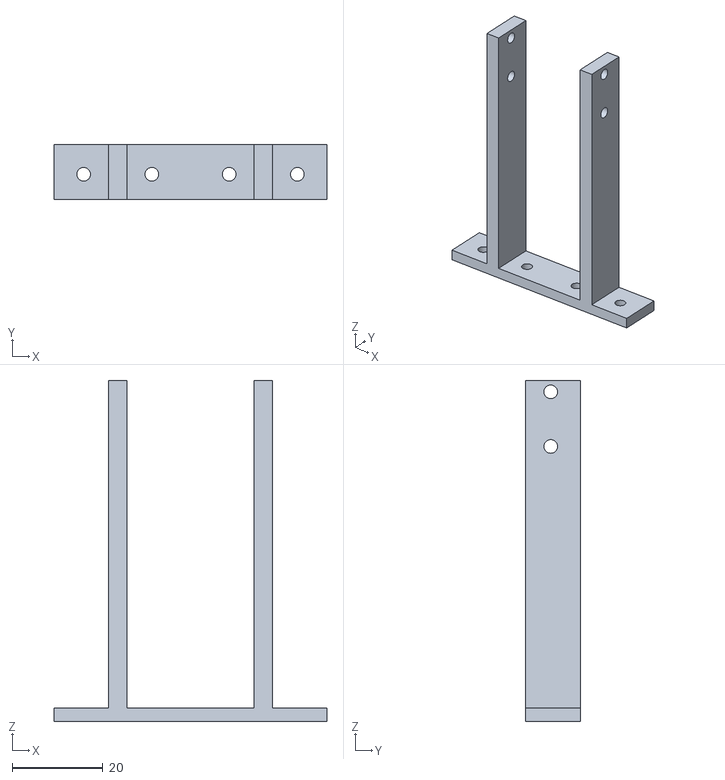
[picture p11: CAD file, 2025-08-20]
design-files/Camera Support.stl
60.0 x 12.0 x 75.0

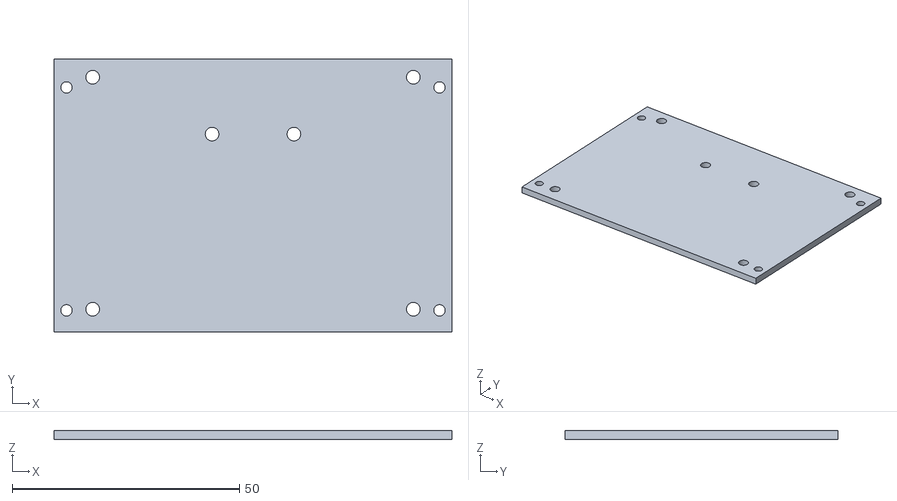
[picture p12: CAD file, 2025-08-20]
design-files/Raspberry Pi and UPS Platform.stl
87.5 x 60.0 x 2.00

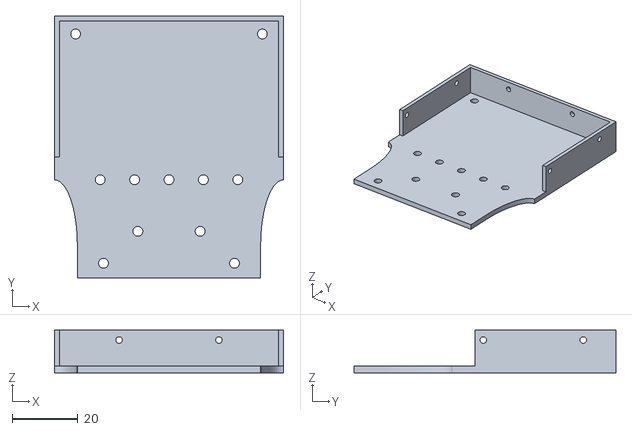
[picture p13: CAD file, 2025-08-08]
design-files/Lidar Holder V2.stl
70.0 x 80.0 x 13.0

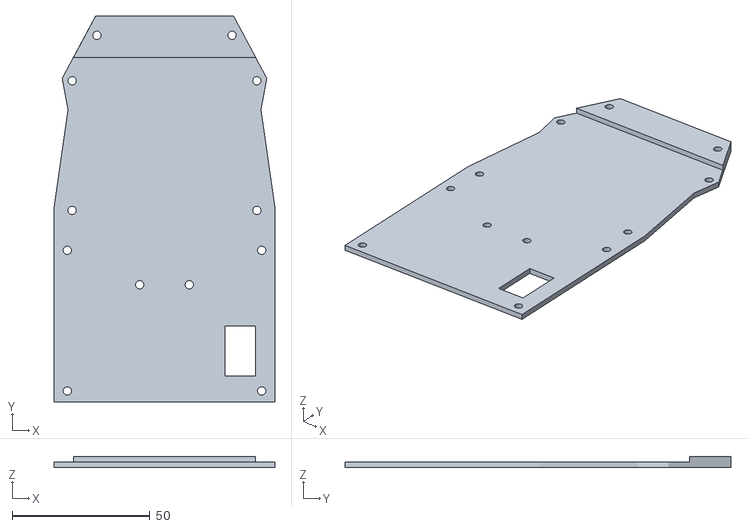
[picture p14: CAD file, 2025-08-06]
design-files/Peripherals Board Middle Plate.stl
80.0 x 140.0 x 4.00

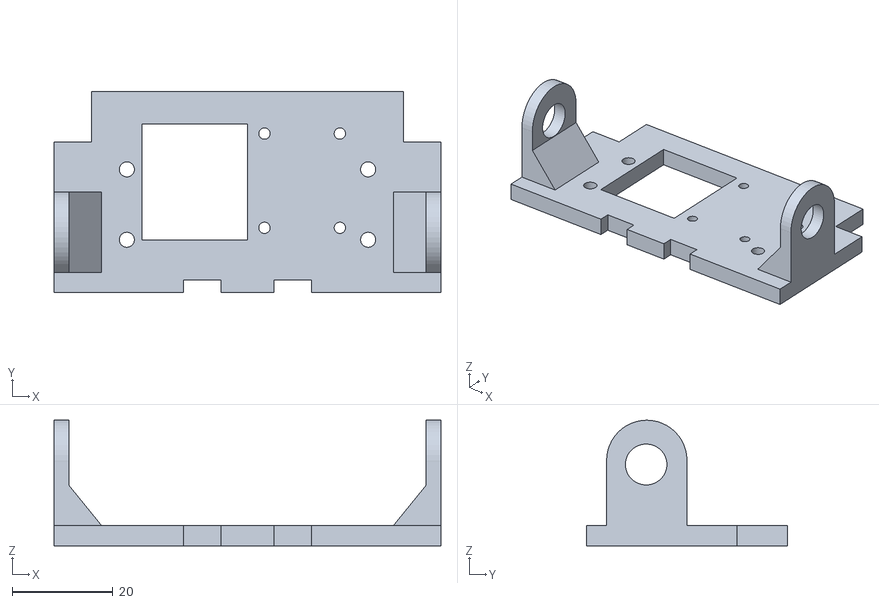
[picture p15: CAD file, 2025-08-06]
design-files/N20 Motor Holder.stl
77.0 x 40.0 x 25.0

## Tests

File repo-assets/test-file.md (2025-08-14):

# Raspberry Pi 4B
## Top
Raspberry Pi 4B Top
## Bottom
Raspberry Pi 4B Bottom
## Top Rotated
Raspberry Pi 4B Top Rotated
## Bottom Rotated
Raspberry Pi 4B Bottom Rotated
# N20 Geared Motor With Encoder
## Top
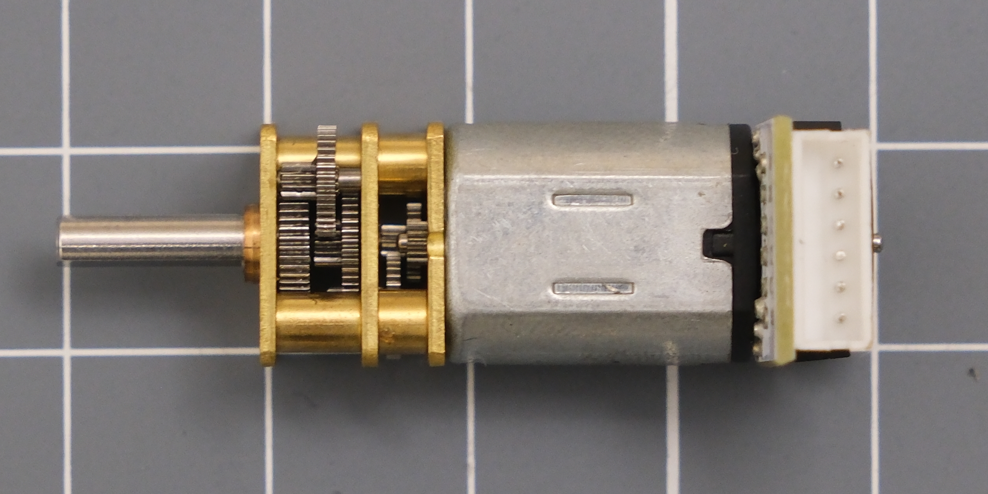
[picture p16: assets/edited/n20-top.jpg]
N20 Geared Motor With Encoder Top

## Side
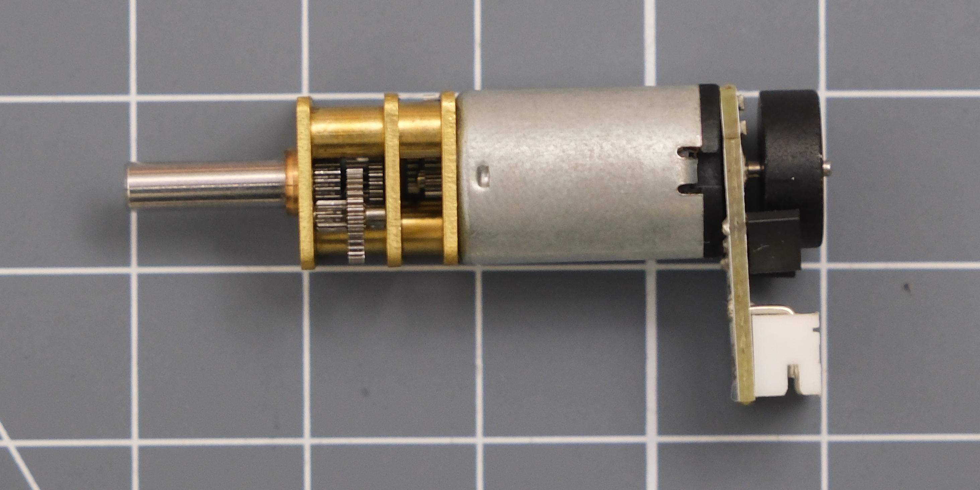
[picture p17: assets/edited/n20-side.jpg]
N20 Geared Motor With Encoder Side

#  TFLuna 1D LiDAR
TFLuna

#  RPLidar
## Top
RPLidar Top
## Bottom
RPLidar Bottom
#  Peripherals Board
## Populated
RPLidar Top
## PCB Top
RPLidar Bottom
## PCB Bottom
RPLidar Bottom
#  Wheels
## Wheels Top
RPLidar Bottom
## Wheels Bottom
RPLidar Bottom

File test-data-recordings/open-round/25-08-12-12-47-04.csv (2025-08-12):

OriX | OriY | OriZ | LidarLeft | LidarFront | LidarRight | CmdSpeed | CmdSteer | IMUSysCal | GyroCal | AccelCal | MagCal | Speed
0.000000 | 0.000000 | 0.000000 | 44.000000 | 105.000000 | 43.000000 | 0.000000 | 90.000000 | 0.000000 | 0.000000 | 0.000000 | 0.000000 | 0.000000
0.000000 | 0.000000 | 0.000000 | 44.000000 | 105.000000 | 43.000000 | 0.000000 | 90.000000 | 0.000000 | 0.000000 | 0.000000 | 0.000000 | 0.000000
0.000000 | 0.000000 | 0.000000 | 44.000000 | 105.000000 | 43.000000 | 0.000000 | 90.000000 | 0.000000 | 0.000000 | 0.000000 | 0.000000 | 0.000000
360.000000 | -1.560000 | -3.120000 | 44.000000 | 105.000000 | 43.000000 | 0.000000 | 90.000000 | 0.000000 | 0.000000 | 0.000000 | 0.000000 | 0.000000
360.000000 | -1.560000 | -3.120000 | 44.000000 | 105.000000 | 43.000000 | 0.000000 | 90.000000 | 0.000000 | 0.000000 | 0.000000 | 0.000000 | 0.000000
0.000000 | -1.560000 | -3.120000 | 44.000000 | 105.000000 | 43.000000 | 0.000000 | 90.000000 | 0.000000 | 0.000000 | 0.000000 | 0.000000 | 0.000000
0.000000 | -1.560000 | -3.120000 | 44.000000 | 105.000000 | 43.000000 | 0.000000 | 90.000000 | 0.000000 | 0.000000 | 0.000000 | 0.000000 | 0.000000
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

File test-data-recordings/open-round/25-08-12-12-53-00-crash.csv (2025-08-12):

OriX | OriY | OriZ | LidarLeft | LidarFront | LidarRight | CmdSpeed | CmdSteer | IMUSysCal | GyroCal | AccelCal | MagCal | Speed
0.000000 | 0.000000 | 0.000000 | 45.000000 | 114.000000 | 43.000000 | 0.000000 | 90.000000 | 0.000000 | 0.000000 | 0.000000 | 0.000000 | 0.000000
0.000000 | 0.000000 | 0.000000 | 45.000000 | 114.000000 | 43.000000 | 0.000000 | 90.000000 | 0.000000 | 0.000000 | 0.000000 | 0.000000 | 0.000000
0.000000 | 0.000000 | 0.000000 | 45.000000 | 115.000000 | 43.000000 | 0.000000 | 90.000000 | 0.000000 | 0.000000 | 0.000000 | 0.000000 | 0.000000
0.000000 | -1.810000 | -3.500000 | 45.000000 | 115.000000 | 43.000000 | 0.000000 | 90.000000 | 0.000000 | 0.000000 | 0.000000 | 0.000000 | 0.000000
0.000000 | -1.810000 | -3.500000 | 45.000000 | 114.000000 | 43.000000 | 0.000000 | 90.000000 | 0.000000 | 0.000000 | 0.000000 | 0.000000 | 0.000000
0.000000 | -1.810000 | -3.500000 | 45.000000 | 113.000000 | 44.000000 | 0.000000 | 90.000000 | 0.000000 | 0.000000 | 0.000000 | 0.000000 | 0.000000
0.000000 | -1.810000 | -3.500000 | 45.000000 | 114.000000 | 43.000000 | 0.000000 | 90.000000 | 0.000000 | 0.000000 | 0.000000 | 0.000000 | 0.000000
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

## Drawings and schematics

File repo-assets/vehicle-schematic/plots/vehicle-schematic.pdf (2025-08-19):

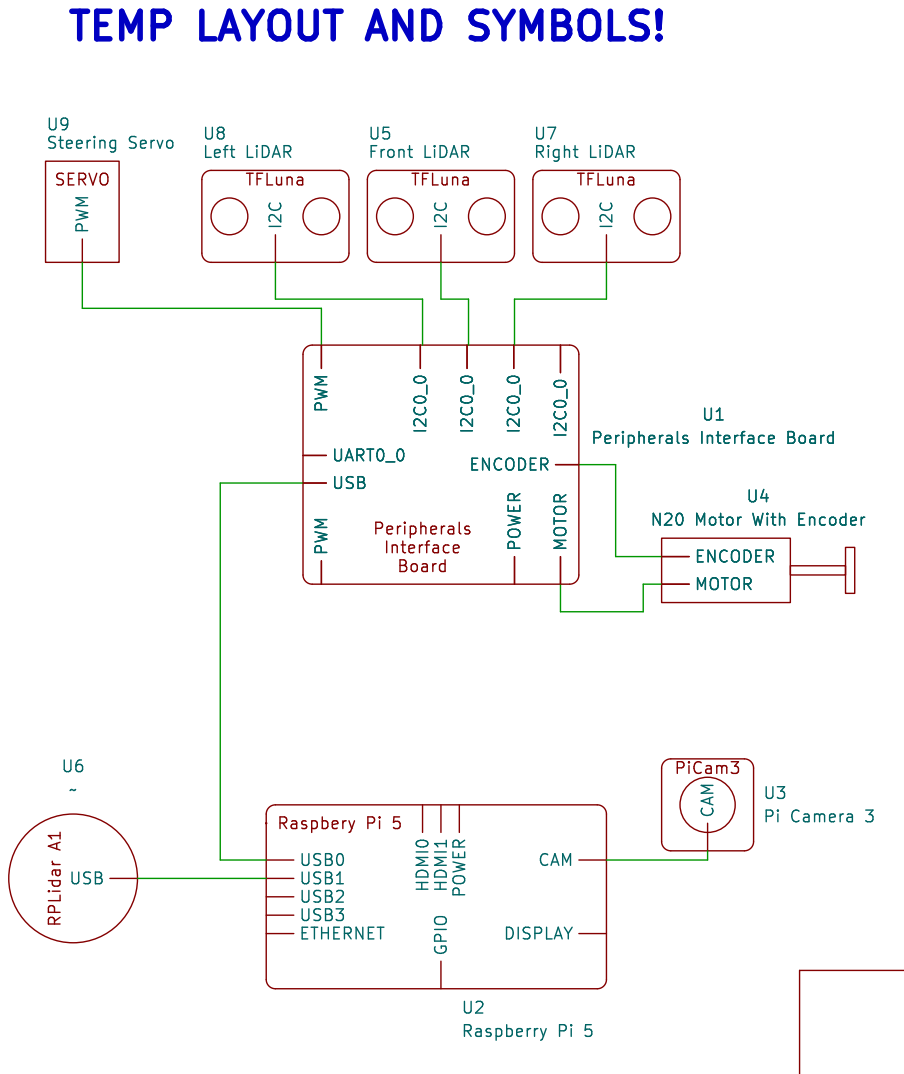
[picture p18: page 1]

U4 N20 Motor With Encoder ENCODER MOTOR

DISPLAY U2 Raspberry Pi 5 Peripherals

Id: 1/1 Title: Vehicle Wiring Overview

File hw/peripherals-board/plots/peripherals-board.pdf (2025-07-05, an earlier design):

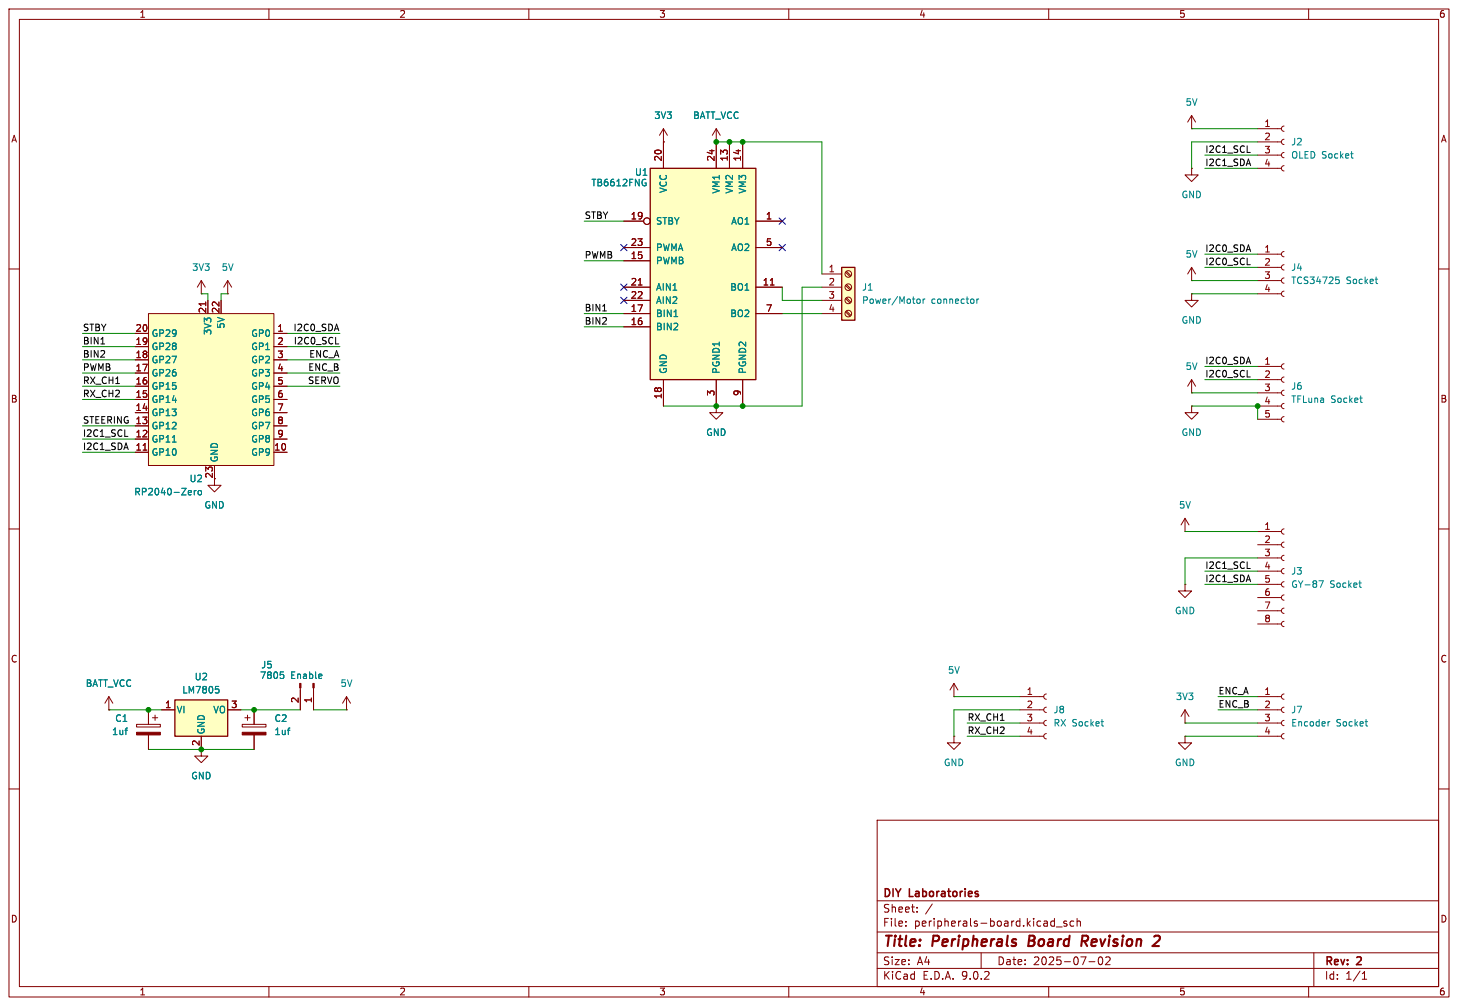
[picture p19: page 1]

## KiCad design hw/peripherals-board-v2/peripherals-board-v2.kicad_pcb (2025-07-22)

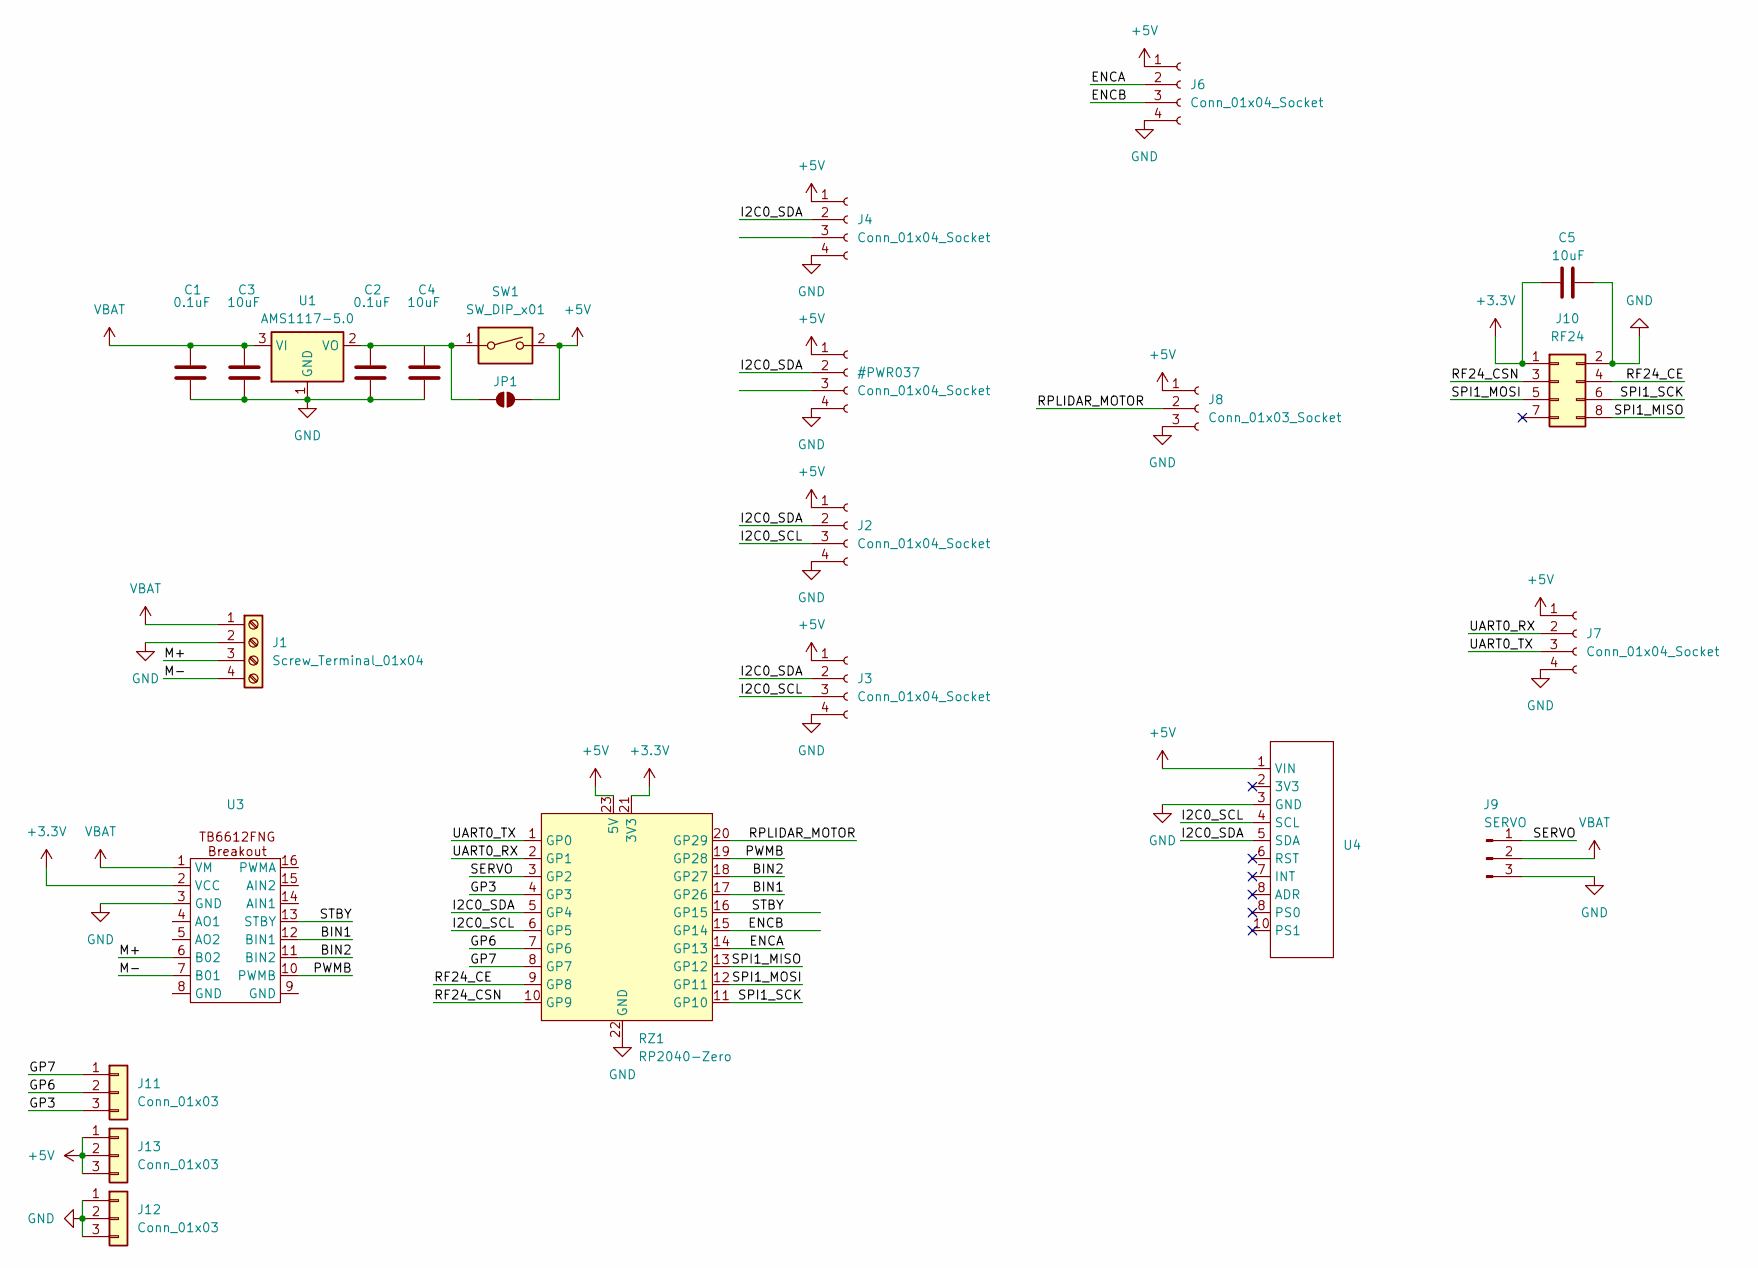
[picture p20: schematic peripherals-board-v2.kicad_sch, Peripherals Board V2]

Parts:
C1, C2: 0.1uF; C_0805_2012Metric_Pad1.18x1.45mm_HandSolder
C3, C4, C5: 10uF; C_0805_2012Metric_Pad1.18x1.45mm_HandSolder
J1: Screw_Terminal_01x04; ScrewTerminal_01x04_P5mm
J2, J3, J4, J6, J7: Conn_01x04_Socket; JST_XH_01x04_Horizontal_NoFlange
J8: Conn_01x03_Socket; JST_XH_01x03_Horizontal_NoFlange
J9: SERVO; PinHeader_1x03_P2.54mm_Vertical
J10: RF24; PinSocket_2x04_P2.54mm_Vertical
J11, J12, J13: Conn_01x03; PinSocket_1x03_P2.54mm_Vertical
JP1: SolderJumper_2_Open; SolderJumper-2_P1.3mm_Open_TrianglePad1.0x1.5mm
RZ1: RP2040-Zero
SW1: SW_DIP_x01; SW_DIP_SPSTx01_Slide_6.7x4.1mm_W7.62mm_P2.54mm_LowProfile
U1: AMS1117-5.0; SOT-223-3_TabPin2
U3: TB6612FNG-breakout
U4: BNO055-breakout

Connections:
+3.3V: C5.1, J10.1, RZ1.21 (3V3), U3.2 (VCC)
/BIN1: RZ1.17 (GP26), U3.12 (BIN1)
/BIN2: RZ1.18 (GP27), U3.11 (BIN2)
/ENCA: J6.2, RZ1.14 (GP13)
/ENCB: J6.3, RZ1.15 (GP14)
/GP3: J11.3, RZ1.4 (GP3)
/GP6: J11.2, RZ1.7 (GP6)
/GP7: J11.1, RZ1.8 (GP7)
/I2C0_SCL: J2.3, J3.3, J4.3, RZ1.6 (GP5), U4.4 (SCL); also elsewhere on the board
/M+: J1.3, U3.6 (B02)
/M-: J1.4, U3.7 (B01)
/PWMB: RZ1.19 (GP28), U3.10 (PWMB)
/RF24_CE: J10.4, RZ1.9 (GP8)
/RF24_CSN: J10.3, RZ1.10 (GP9)
/RPLIDAR_MOTOR: J8.2, RZ1.20 (GP29)
/SERVO: J9.1, RZ1.3 (GP2)
/SPI1_MISO: J10.8, RZ1.13 (GP12)
/SPI1_MOSI: J10.5, RZ1.12 (GP11)
/SPI1_SCK: J10.6, RZ1.11 (GP10)
/STBY: RZ1.16 (GP15), U3.13 (STBY)
/UART0_RX: J7.2, RZ1.2 (GP1)
/UART0_TX: J7.3, RZ1.1 (GP0)
unnamed: C2.1, C4.1, JP1.1 (A), SW1.1, U1.2 (VO)
VBAT: C1.1, C3.1, J1.1, J9.2, U1.3 (VI), U3.1 (VM)

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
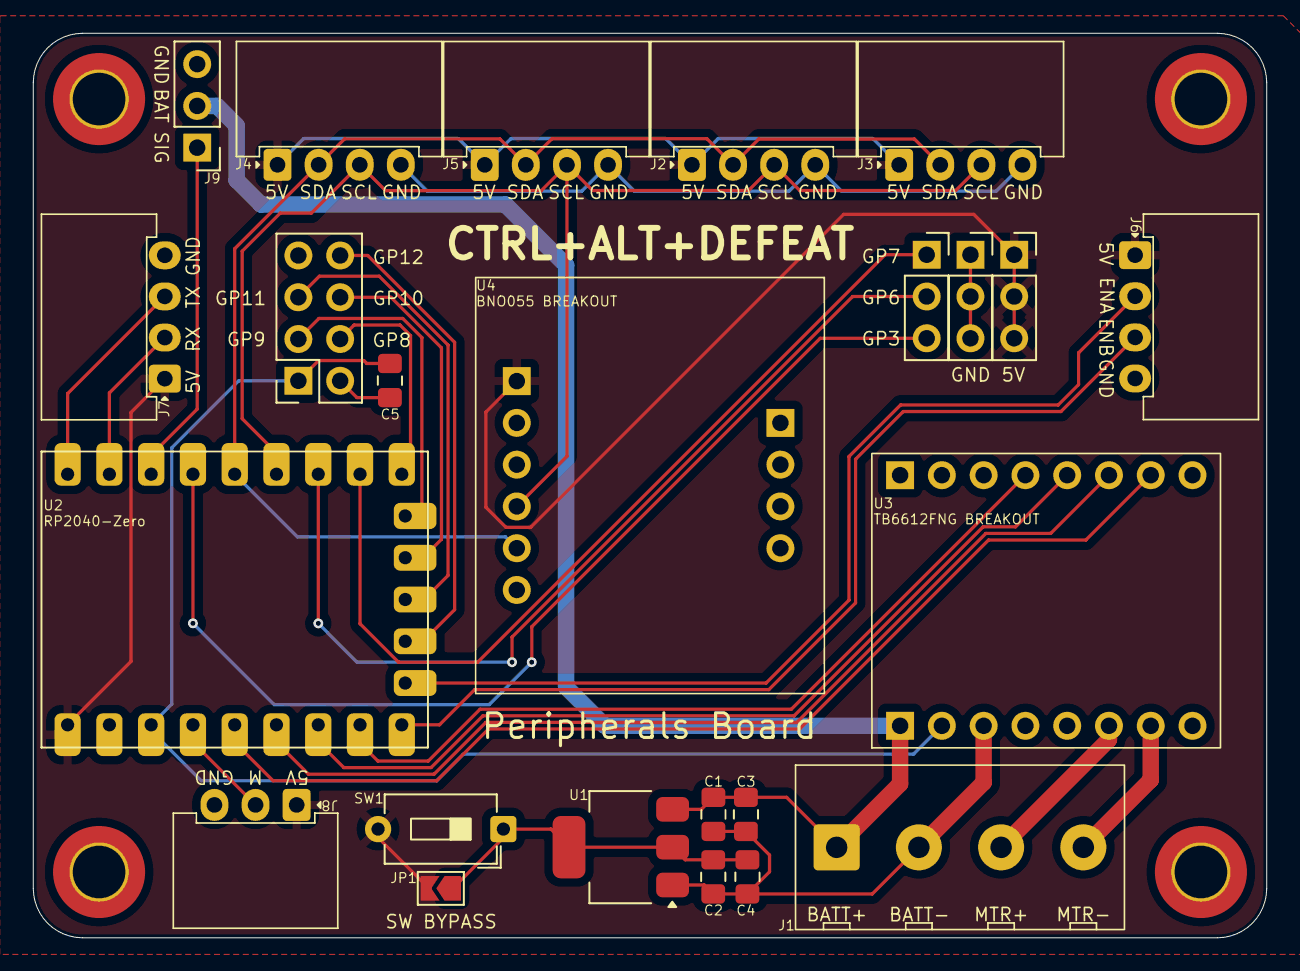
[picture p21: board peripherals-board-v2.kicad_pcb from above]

Board: 2 copper layers, 75.0 x 55.0 mm, 24 parts (0 on the bottom side), 27 nets.

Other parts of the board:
J5: Conn_01x04_Socket; JST_XH_01x04_Horizontal_NoFlange

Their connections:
/I2C0_SCL: J5.3; also elsewhere on the board

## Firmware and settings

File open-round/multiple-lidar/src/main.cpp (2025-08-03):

/* __ This Code Will Not Work __
We later realised that the BNO055 IMU does not have a proper I2C protocol, so it can't be used on the same bus as the TFLuna LiDARs.
The Arduino has only 1 I2C bus, while the RP2040, later used, has 2 enabling this system to work (with different PinOuts)
*/

#include <Arduino.h>

#include <Wire.h>

#include <Adafruit_Sensor.h>
#include <Adafruit_BNO055.h>
#include <utility/imumaths.h>
#include <Servo.h>
#include <TFLI2C.h>
#include <SoftwareSerial.h>

const byte rxPin = 9;
const byte txPin = 11;

// Set up a new SoftwareSerial object
SoftwareSerial mySerial (rxPin, txPin);
TFLI2C lidar;
Servo myservo;

// Pin definitions
const int encoder1 = 2;
const int encoder2 = 3;
const int startBtn = 5;
const int motor = 12;
const int motorDir = 10;

// About driving
int dir = 1;
int lastEncoded = 0; 
long encoderValue = 0;
float distance = 0.0;

// About turning
int turns = 0;
bool turning = false;
int turnDir = 0;           // 1 for clockwise, -1 for counterclockwise

// About IMU
Adafruit_BNO055 bno = Adafruit_BNO055(0x28);
float yaw;
int targetYaw = 0;
int startYaw = 0;

unsigned long startMillis;
unsigned long currentMillis;
const unsigned long period = 200;

int pos = 90;    // variable to store the servo position  

// About Lidar
int threshold = 60;
int16_t front_lidarDist;
int16_t left_lidarDist;
int16_t right_lidarDist;
int16_t front_startDist = 50;
int16_t left_startDist = 40;
int16_t right_startDist = 40;
int stopDist = 5;

// About Gyro straight follower
int correction = 0;
float error = 0;
float totalError = 0;             // Used for integral control
float lateral_error = 0;          // Used for lateral correction
float width = 80;                // Width of track as seen by Lidars

// Function declarations
void updateEncoder();
void forward(int pwm);
void backward(int pwm);
void stop();
void steer(int angle);
void checkYaw();
void pStraight();

void setup() {
  // put your setup code here, to run once:
  Serial.begin(9600);
  mySerial.begin(9600);
  Wire.begin(); 
  myservo.attach(9);
  myservo.write(90);

  pinMode(startBtn, INPUT_PULLUP);

  pinMode(motor, OUTPUT); 
  pinMode(motorDir, OUTPUT); 
  pinMode(encoder1, INPUT_PULLUP); 
  pinMode(encoder2, INPUT_PULLUP);
  
  attachInterrupt(digitalPinToInterrupt(2), updateEncoder, CHANGE); 
  attachInterrupt(digitalPinToInterrupt(3), updateEncoder, CHANGE);
  
  while (true){
    int pinValue = digitalRead(startBtn);
    mySerial.println("Waiting");
    if(pinValue != 1){
      Serial.println("Started");
      break;
    }
  }
  delay(1500);

  if(!bno.begin()){
    Serial.print("Ooops, no BNO055 detected ... Check your wiring or I2C ADDR!");
  }
  bno.setExtCrystalUse(true);
  Serial.println("Initializing...");
  
  lidar.getData(left_startDist, 0x30);
  lidar.getData(right_startDist, 0x10);
  lidar.getData(front_startDist, 0x20);
  Serial.print("Start Distance: ");
  Serial.println(front_startDist);
  if (front_startDist > 140) stopDist = 0;
  else stopDist = 80;
  
  forward(240);
}

void loop() {
  // put your main code here, to run repeatedly:
  
  sensors_event_t event; 
  bno.getEvent(&event);

  yaw = event.orientation.x;

  distance = encoderValue / 45;
  
  lidar.getData(left_lidarDist, 0x30);
  lidar.getData(right_lidarDist, 0x10);
  lidar.getData(front_lidarDist, 0x20); 
  
  currentMillis = millis();
  if (currentMillis - startMillis >= period){
    startMillis = currentMillis;
    
    //Serial.print(" Yaw:");
    mySerial.print(yaw);
    mySerial.print(',');
    //Serial.print("Front:");
    mySerial.print(front_lidarDist);
    mySerial.print(',');
    //Serial.print("Left:");
    mySerial.print(left_lidarDist);
    mySerial.print(',');
    //Serial.print("Right:");
    mySerial.println(right_lidarDist);
    
    /*Serial.print(" Target Yaw:");
    Serial.print(targetYaw);
    
    Serial.print(" Encoder Value:");
    Serial.print(encoderValue);

    Serial.print(" Distance:");
    Serial.print(distance);

    Serial.print(" Direction:");
    Serial.print(dir);

    Serial.print(" Turns:");
    Serial.println(turns);*/
  }

  checkYaw();
  
  if ((front_lidarDist < threshold) && (turning == false) && (turns == 0 or distance > 100)){
    steer(90);
    turning = true;
  }
  if ((turnDir == 0) && (left_lidarDist > left_startDist + 50)) turnDir = -1; // Turning to left
  else if ((turnDir == 0) && (right_lidarDist > right_startDist + 50)) turnDir = 1; // Turning to right
  
  if (turns == 12 && distance >= stopDist){ 
    stop();
    myservo.write(90);
    while (true){}
  }

  pStraight();
  delay(0.5);
}

// put function definitions here:
void updateEncoder(){
  if(dir == -1) encoderValue --;
  if(dir == 1) encoderValue ++;
}

void forward(int pwm){
  dir = 1;
  digitalWrite(motorDir,HIGH);
  analogWrite(motor,pwm);
}

void backward(int pwm){
  dir = -1;
  digitalWrite(motorDir,LOW);
  analogWrite(motor,pwm);
}

void stop(){
  digitalWrite(motor,0);
  digitalWrite(motorDir,LOW);
}

void steer(int angle){
  myservo.write(90 + turnDir*42);
  forward(225);
  startYaw = yaw;
  targetYaw = yaw + angle*turnDir;
  if (targetYaw > 360) targetYaw = targetYaw - 360;
  if (targetYaw > 75 && targetYaw < 105) targetYaw = 90;
  else if (targetYaw > 165 && targetYaw < 195) targetYaw = 180;
  else if (targetYaw > 255 && targetYaw < 285) targetYaw = 270;
  else if (targetYaw > 345 or targetYaw < 15) targetYaw = 0;
}

void checkYaw(){
  float difference = targetYaw - yaw;
  if (abs(difference) <= 6 && turning == true){
    myservo.write(90);
    forward(275);
    turning = false;
    encoderValue = 0;
    distance = 0;
    turns ++;
  }
}

void pStraight(){
  if(turning == false){
    correction = 0;
    lateral_error = 0;
    error = round(targetYaw - yaw);
    width = right_lidarDist + left_lidarDist;
    if (width > 80) width = 80;
    lateral_error = right_lidarDist - left_lidarDist; // Calculate lateral error based on lidar readings
    
    if (error > 180) error = error - 360;
    else if (error < -180) error = error + 360;                     // Normalize error to [-180, 180]
    totalError += error;                                            // Accumulate error for integral control
    
    if (error > 0) correction = error * 2.3 - totalError * 0.001; // correction to the right based on yaw
    else if (error < 0) correction = error * 2.2 - totalError * 0.001; // correction to the left based on yaw

    if (lateral_error > 0) correction += lateral_error * 0.55; // correction to left based on lateral error
    else if (lateral_error < 0) correction += lateral_error * 0.5; // correction to right based on lateral error

    if (correction > 45) correction = 45;
    else if (correction < -45) correction = -45;

    myservo.write(90 + correction);
    //Serial.print("Correction: ");
    //Serial.print(correction);
  }
}

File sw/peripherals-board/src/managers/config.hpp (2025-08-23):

/**
 * @file configuration.hpp
 * @brief Defines various structs for holding configuration data
 * @author DIY Labs
 */

 #pragma once

#include <cstdint>

class PowertrainDriver;

/**
 * @brief Phsyical pin numbers for peripherals
 */
struct PinConfig{

  uint8_t motorDriverPWM = 0;
  uint8_t motorDriverDirA = 0;
  uint8_t motorDriverDirB = 0; 
  uint8_t motorDriverStandby = 0;

  uint8_t motorEncoderA = 0;
  uint8_t motorEncoderB = 0;

  uint8_t steeringServo = 0;
  
  uint8_t nrfCS = 0;
  uint8_t nrfCE = 0;

  uint8_t i2c0SDA = 0;
  uint8_t i2c0SCL = 0;
  uint8_t i2c1SDA = 0;
  uint8_t i2c1SCL = 0;

  uint8_t spi0MOSI = 0;
  uint8_t spi0MISO = 0;
  uint8_t spi0SCK = 0;  

  uint8_t spi1MOSI = 0;
  uint8_t spi1MISO = 0;
  uint8_t spi1SCK = 0;  

  uint8_t uart0RX = 0;
  uint8_t uart0TX = 0;

  uint8_t uart1RX = 0;
  uint8_t uart1TX = 0;

  uint8_t lidarMotorPWM = 0;

  uint8_t rgbLed;

};

struct LimitsConfig{

  uint16_t maxForwardSpeed = 0;
  uint16_t maxReverseSpeed = 0;

  uint16_t servoMinOutput = 0;
  uint16_t servoMaxOutput = 0;
  uint16_t servoCenterOutput = 0;

};

struct ConstantsConfig{

  uint8_t ticksPerCM = 0;
  uint32_t debugSerialBaudRate = 0;
  uint32_t rpiSerialBaudRate = 0;

};

struct AddressConfig{

  uint8_t bnoAddr = 0;
  uint8_t leftLidarAddr = 0;
  uint8_t frontLidarAddr = 0;
  uint8_t rightLidarAddr = 0;
  uint8_t backLidarAddr = 0;

};

struct ControlConfig{

  double steeringP = 0;
  double steeringI = 0;
  double steeringD = 0;
  double maxSteeringPIDCommand = 0;
  double minSteeringPIDCommand = 0;

  double speedP = 0;
  double speedI = 0;
  double speedD = 0;
  double maxSpeedPIDCommand = 0;
  double minSpeedPIDCommand = 0;

  double maxSteeringAngle = 0;

  float servoCommandToOutputRatio = 1; // 1 to avoid division by zero errors
};

/**
 * @brief One Config Struct To Rule Them All
 */
struct VehicleConfig{

  PinConfig pinConfig;
  LimitsConfig limitsConfig;
  ConstantsConfig constantsConfig;
  AddressConfig addressConfig;
  ControlConfig controlConfig;

};

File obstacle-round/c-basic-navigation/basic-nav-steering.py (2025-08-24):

'''
This does not work, refer to basic-nav-v2.py

This is a program to test a basic straight drive of the robot over 3 sections
There is no turning algorithm here
'''

import cv2
import numpy as np
from picamera2 import Picamera2
import time
import serial
import math
import RPi.GPIO as GPIO

# Status LED
led = 17
GPIO.setmode(GPIO.BCM)
GPIO.setup(led, GPIO.OUT)

#Camera config
tuning = Picamera2.load_tuning_file("imx219.json")
picam2 = Picamera2(tuning = tuning)
config = picam2.create_video_configuration(main={"size": (1280, 720)})
picam2.configure(config)
picam2.start_preview()
GPIO.output(led, GPIO.HIGH)
time.sleep(1.5)  # Let the camera warm up
GPIO.output(led, GPIO.LOW)
picam2.start()

# Serial config
# usb-Raspberry_Pi_Pico_E6625887D3859130-if00 - Pranav
# usb-Raspberry_Pi_Pico_E6625887D3482132-if00 - Adbhut
ser = serial.Serial('/dev/serial/by-id/usb-Raspberry_Pi_Pico_E6625887D3859130-if00', 115200, timeout=1)


# Some starting values
yaw, target_yaw, total_error, distance = 0, 0, 0, 0
left_dist, front_dist, right_dist = 35, 100, 35
turns, turning = 0, False
prev_dist, min_dist, prev_str = 0, 0, 90

#Define colour ranges
lower_red = np.array([0, 120, 88])
upper_red = np.array([19, 255, 255])
lower_green = np.array([52, 120, 78])
upper_green = np.array([70, 255, 255])
lower1_black = np.array([37, 65, 20])
upper1_black = np.array([65, 130, 60])
lower2_black = np.array([40, 130, 50])
upper2_black = np.array([49, 175, 90])
# The 'magenta' parking pieces also show up as red!

# Related to obstacles
red_obs = [[[0,0,0,0],[0,0,0]]]
green_obs = [[[0,0,0,0],[0,0,0]]]
all_prev_obs = []
all_obs = []
prev_obs = [[0,0,0,0],'']
corner_obs =  ''
obs_passed_dist = 0
dist_from_passed_obs = 0

def process_frame():
    global hsv_frame, hsv_roi, corrected_frame
    global all_obs, all_prev_obs, red_obs, green_obs

    # Create a mask to detect colours
    mask_red = cv2.inRange(hsv_roi, lower_red, upper_red)
    mask_green = cv2.inRange(hsv_roi, lower_green, upper_green)
    #mask_black = cv2.inRange(hsv_roi, lower1_black, upper1_black) + cv2.inRange(hsv_roi, lower2_black, upper2_black)
    
    # Find contours for red and green. We don't want the hierarchy
    red_contours, _ = cv2.findContours(mask_red, cv2.RETR_EXTERNAL, cv2.CHAIN_APPROX_SIMPLE)
    green_contours, _ = cv2.findContours(mask_green, cv2.RETR_EXTERNAL, cv2.CHAIN_APPROX_SIMPLE)
    #black_contours, _ = cv2.findContours(mask_black, cv2.RETR_EXTERNAL, cv2.CHAIN_APPROX_SIMPLE)

    # Filter and locate obstacle bounding boxes
    red_obs = get_obstacle_positions(red_contours, red_obs)
    green_obs = get_obstacle_positions(green_contours, green_obs)

    all_prev_obs = all_obs
    all_obs = []
    for obs in red_obs, green_obs:
        all_obs.append(obs)
    all_obs.sort(key=lambda obs: obs[0][1])

    if len(all_prev_obs)-len(all_obs)>0:
        for obs in all_prev_obs:
            if abs(600-obs[0][0]) > 500: 
                corner_obs = obs 
                print(f"{corner_obs} corner obs passed out of view")

    # Draw contours for visualization
    #print(f"Red Obs: {red_obs}")
    #print(f"Green Obs: {green_obs}")

    # Draw rectangles around object for checking
    for item in red_obs:
        x = item[0][0]
        y = item[0][1] + 350    #ROI was cropped
        w = item[0][2]
        h = item[0][3]
        cv2.rectangle(corrected_frame, (x,y), (x+w,y+h), (0,255,0), 2)
    for item in green_obs:
        x = item[0][0]
        y = item[0][1] + 350    # ROI was cropped
        w = item[0][2]
        h = item[0][3]
        cv2.rectangle(corrected_frame, (x,y), (x+w,y+h), (0,255,0), 2)

    return corrected_frame, red_obs, green_obs

def get_obstacle_positions(contours, obs):
    obs = []
    min_area = 500      # minimum contour area to be obstacle in pixels
    max_area = 30000    # largest obstacle size possible

    for cnt in contours:
        if cv2.contourArea(cnt) > min_area and cv2.contourArea(cnt) < max_area:
            x,y,w,h = cv2.boundingRect(cnt)
            if h > w:
                # TODO when driving integration done; Second tuple gives grid pos
                obs.append([[x,y,w,h], [0,0,0]]) 
    if obs == []: obs = [[[0,0,0,0],[0,0,0]]]           
    return obs

def nearest_obstacle():
    global red_obs, green_obs

    nearest_obs = [[0,0,0,0],'']
    for obs in red_obs: 
        if nearest_obs[0][1] < obs[0][1]: 
            nearest_obs = obs
            nearest_obs[1] = 'red'
    for obs in green_obs: 
        if nearest_obs[0][1] < obs[0][1]: 
            nearest_obs = obs
            nearest_obs[1] = 'green'
    print(f'Nearest obstacle is {nearest_obs[1]} at {nearest_obs[0]}')
    return nearest_obs
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

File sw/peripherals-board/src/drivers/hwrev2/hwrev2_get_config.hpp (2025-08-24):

/**
 * @brief Implements function to get configuration struct
 * @author DIY Labs
 */

#pragma once

#include <managers/config.hpp>

/**
 * @brief Returns vehicle configuration struct for hardware revision 2
 * @return Vehicle configuration struct for hardware revision 2
 */
VehicleConfig hwrev2_getConfig(){

  VehicleConfig cfg;

  cfg.pinConfig.motorDriverDirA             = 26;
  cfg.pinConfig.motorDriverDirB             = 27;
  cfg.pinConfig.motorDriverPWM              = 28;
  cfg.pinConfig.motorDriverStandby          = 15;
  cfg.pinConfig.steeringServo               = 2;

  cfg.pinConfig.motorEncoderA               = 13;
  cfg.pinConfig.motorEncoderB               = 14;

  cfg.pinConfig.uart0RX                     = 1;
  cfg.pinConfig.uart0TX                     = 0;

  cfg.pinConfig.nrfCE                       = 8;
  cfg.pinConfig.nrfCS                       = 9;
  cfg.pinConfig.spi1MISO                    = 12;
  cfg.pinConfig.spi1MOSI                    = 11;
  cfg.pinConfig.spi1SCK                     = 10;

  cfg.pinConfig.i2c0SDA                     = 4;
  cfg.pinConfig.i2c0SCL                     = 5;

  cfg.pinConfig.uart0RX                     = 1;
  cfg.pinConfig.uart0TX                     = 0;

  cfg.pinConfig.rgbLed                      = 16;

  cfg.limitsConfig.maxForwardSpeed          = 500;
  cfg.limitsConfig.maxForwardSpeed          = 500;

  cfg.constantsConfig.ticksPerCM            = 40;
  cfg.constantsConfig.debugSerialBaudRate   = 921600;
  cfg.constantsConfig.rpiSerialBaudRate     = 115200;

  cfg.addressConfig.bnoAddr                 = 0x28;
  cfg.addressConfig.leftLidarAddr           = 0x10;
  cfg.addressConfig.frontLidarAddr          = 0x20;
  cfg.addressConfig.rightLidarAddr          = 0x30;
  cfg.addressConfig.backLidarAddr           = 0x40;

  cfg.controlConfig.steeringP               = 5.0;
  cfg.controlConfig.steeringI               = 0.5;
  cfg.controlConfig.steeringD               = 0.5;

  cfg.controlConfig.speedP                  = 1.0;
  cfg.controlConfig.speedI                  = 0.1;
  cfg.controlConfig.speedD                  = 0.1;

  cfg.controlConfig.maxSteeringPIDCommand   = 200.0;
  cfg.controlConfig.minSteeringPIDCommand   = -200.0;

  cfg.controlConfig.maxSteeringAngle        = 45.0; 

  return cfg;
  
}

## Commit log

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2025-07-01 Create KiCad project for peripherals board
    [peripherals-board.kicad_pcb, peripherals-board.kicad_sch]
2025-07-01 Add components to KiCad schematic, update .gitignore
    [peripherals-board.kicad_sch]
2025-07-02 Change to RP2040-Zero symbol, create Processing sketch for telemetry viewer
    [peripherals-board.kicad_sch]
2025-07-02 Make connections in schematic
    [peripherals-board.kicad_sch]
2025-07-03 Add design file for motor holder
    [N20 Motor Holder.stl]
2025-07-04 Add files via upload
    Adding program for control of N20 motor with HW-723 Shield for Arduino
2025-07-04 Add files via upload
    Adding test files for BNO055 gyroscope, accelerometer and magnetometer
2025-07-05 Update schematic to match board
    [peripherals-board.kicad_sch]
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2025-07-05 Add files via upload
    Adding files for testing of all sensors and motors with Arduino with Motor controller shield, servo, lidar and IMU
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2025-07-06 First program for open round
    First program for open round using Arduino, TFLuna Lidar, IMU and chassis
2025-07-07 Create KiCad project for Peripherals Board V2
    [peripherals-board-v2.kicad_pcb, peripherals-board-v2.kicad_sch]
2025-07-07 Add library for RP2040-zero
    [peripherals-board-v2.kicad_sch]
2025-07-09 Create symbol and footprint for TB6612 breakout board
    [peripherals-board-v2.kicad_pcb, peripherals-board-v2.kicad_sch]
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2025-07-09 Create symbol and footprint for GY-87
    [peripherals-board-v2.kicad_sch]
2025-07-09 Link GY87 footprint to symbol
    [peripherals-board-v2.kicad_sch]
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2025-07-10 Revision 1 of PCB layout, create footprints, generate interactive BOM
    [peripherals-board-v2.kicad_pcb, peripherals-board-v2.kicad_sch]
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2025-07-10 Change URL to lowercase
    [peripherals-board-v2.kicad_pcb]
2025-07-10 Create fill both layers for 5v and GND
    [peripherals-board-v2.kicad_pcb]
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2025-07-11 Routing changes to connect vreg to 5v plane
    [peripherals-board-v2.kicad_pcb]
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2025-07-11 Fixing stopping and steering issues
    [main.cpp]
2025-07-11 Reroute PCB
    [peripherals-board-v2.kicad_pcb, peripherals-board-v2.kicad_sch]
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2025-07-12 Design for TFLuna lidar holder for front of chassis
    [Lidar Holder.stl]
2025-07-13 Swap left LiDAR and radio input connectors
    [peripherals-board-v2.kicad_pcb, peripherals-board-v2.kicad_sch]
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2025-07-14 Create footprint and symbol for BNO055 breakout, prototype new layout
    [peripherals-board-v2.kicad_pcb]
2025-07-14 Add connector for RPLidar in schematic
    [peripherals-board-v2.kicad_sch]
2025-07-15 Update peripherals board schematic and layout
    [peripherals-board-v2.kicad_pcb, peripherals-board-v2.kicad_sch]
2025-07-15 Attempt to rescue schematic
    [peripherals-board-v2.kicad_pcb, peripherals-board-v2.kicad_sch]
2025-07-15 Export gerber files, update interactive BOM
    [peripherals-board-v2-B_Cu.gbr, peripherals-board-v2-B_Mask.gbr, peripherals-board-v2-B_Paste.gbr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]
2025-07-15 Change silkscreen, regenerate gerber and ibom
    [peripherals-board-v2-B_Cu.gbr, peripherals-board-v2-B_Mask.gbr, peripherals-board-v2-B_Paste.gbr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]
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2025-07-15 Add reference designators to silkscreen
    [peripherals-board-v2-B_Cu.gbr, peripherals-board-v2-B_Mask.gbr, peripherals-board-v2-B_Paste.gbr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]
2025-07-16 Generate drill files flor PCB
    [peripherals-board-v2-B_Cu.gbr, peripherals-board-v2-B_Mask.gbr, peripherals-board-v2-B_Paste.gbr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]
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2025-07-20 Replace heartbeat data with millis()
    [main.cpp]
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2025-07-20 Add delay to improve issues
    [main.cpp]
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2025-07-29 Create Bill of Materials
    Contains Bill of Materials organised into classifications of chassis, and the 2 systems
2025-07-29 Update rear drive section design
    [N20 Motor Holder.stl]
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2025-08-03 Multiple LiDARs won't work with Arduino
    [main.cpp]
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2025-08-05 Change uint16_t to int16_t to avoid underflowing, add temp code to drive from external radio
    [main.cpp]
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2025-08-05 Update design files
    [N20 Motor Holder.stl, Peripherals Board Middle Plate.stl]
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2025-08-06 Update design files for rear drive and middle section
    [N20 Motor Holder.stl, Peripherals Board Middle Plate.stl, RPLidar Support.stl]
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2025-08-08 Updated frront 1D and 2D Lidars' holder
    [Lidar Holder V2.stl]
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2025-08-10 Open round trial with fixed direction
    [hwrev2_single_lidar_open_round.cpp, hwrev2_single_lidar_open_round.hpp]
2025-08-10 Inhibit speed, reverse encoder position
    [hwrev2_vehicle_speed.cpp]
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2025-08-10 Fix encoder value data reading
    [hwrev2_single_lidar_open_round.cpp]
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2025-08-12 Send buggy vehicle speed over radio
    [main.cpp]
2025-08-12 Add file extension to data file
    [25-08-12-12-47-04.csv]
2025-08-12 Commit more test recordings
    [25-08-12-12-53-00-crash.csv, 25-08-12-13-07-45-hit-inner-wall.csv]
2025-08-12 Commit run data
    [25-08-12-13-25-25-three-rounds-updated-algorithm.csv, 25-08-12-13-41-00-three-rounds-close-to-edge.csv, 25-08-12-13-49-42-hit-on-first-turn.csv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]
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2025-08-13 Update README, forgot to upload design file earlier
    [Raspberry Pi Platform.stl]
2025-08-13 Update BoM and delete old files
    [Lidar Holder.stl]
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2025-08-16 Remove unnecessary zeroes from data
    [25-08-12-13-54-20-hit-on-first-turn-after-calibration.csv, 25-08-12-13-57-20-hit-inner-wall.csv, 25-08-12-14-35-00-hit-inner-wall-distance.csv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]
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2025-08-17 Create symbols for vehicle wiring schematic
    [vehicle-schematic.kicad_pcb, vehicle-schematic.kicad_sch]
2025-08-17 Create temporary symbols and layout for vehicle wiring schematic
    [vehicle-schematic.kicad_sch]
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2025-08-19 Commit broken driver
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2025-08-19 Invert encoder
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2025-08-20 Rename folder for standardisation
    [Lidar Holder V2.stl, N20 Motor Holder.stl, Peripherals Board Middle Plate.stl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]
2025-08-20 New design files for holding the PiCamera and UPS Hat
    [Camera Support.stl, PiCam3 Holder.stl, RPLidar Support.stl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]
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2025-08-22 Add LiDAR to the back too for parking
    [Rear Lidar Mount.stl]
2025-08-22 Directions to pass obstacles were wrong
    [basic-nav-steering.py, detecting-obstacles.py]
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2025-08-23 Repeated crash/hangs on RP2040
    [hwrev2_vehicle_speed.cpp, main.cpp]
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2025-08-24 Modify checklist, loose connection on RP2040 carrier is not relevant with soldered PCB
2025-08-24 Add instruction field to VehicleCommand, fix text error in LiDAR debug log
    [hwrev2_lidar.cpp]
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
